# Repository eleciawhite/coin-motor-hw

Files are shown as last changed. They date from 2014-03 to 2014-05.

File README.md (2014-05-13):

coin-motor-hw (Motor Driver Passthrough)
=============
This repository carries the information for fabricating a board that can drive 
a motor with a MOSFET (and pass through other signals)

Some expository and description can be found here: 
http://www.logicalelegance.com/journey/2014/03/releasing-boards/

The original schematic can be found via DigiKey's SchemeIt (which does not 
have layout capabilities at this time):
http://www.digikey.com/schemeit/#fba

The layout was done by Casey Kikendall. (Thank you!)

Pin out:
1 - motor signal
2 - ground
3 - power
4 - passA (I2C SDA)
5 - passB (I2C SCL)

With the N-Channel MOSFET specified in the BOM, a 5V motor can draw a constant 
~270mA (@25C, 210mA @70C). Pulsing the FET or using a higher voltage can lead 
to higher current throughput.

While the MOSFET can pass 60V on the drain side, it turns on at 2V on the 
gate side. (It can go to 20V on the gate side, though I'm driving it with a 
3.3V low current source GPIO.)

This board was designed to work with a 2.7-3.3 V coin-cell style motor (see 
BOM for link to datasheet). This motor has a start up current of 120mA (max) 
and 90mA normal. A more powerful motor could be used with this board.

The pass through signals are (for my project) used for I2C communication to 
a series of accelerometers. However, the are any signals you want to pass 
through.

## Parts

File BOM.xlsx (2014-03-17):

Name | Digikey PN | Quantity | Cost (1) | Link | Note
Motor | 28821-ND | 1 | 3.99 | http://www.digikey.com/product-detail/en/28821/28821-ND/3083191
Schottkey diode | MBRS130LFSCT-ND | 1 | 0.45 | http://www.digikey.com/product-detail/en/MBRS130L/MBRS130LFSCT-ND/3042645
MOSFET | DMN65D8L-7DICT-ND | 1 | 0.17 | http://www.digikey.com/product-detail/en/DMN65D8L-7/DMN65D8L-7DICT-ND/3677916
50kOhm resistor | RMCF1206FT49K9CT-ND | 1 | 0.06 | http://www.digikey.com/scripts/DkSearch/dksus.dll?Detail&itemSeq=146430875&uq=635306656020798143 | Many options, this isn't quite the cheapest
Connectors | 952-2328-ND | 3 | 0.14 | http://www.digikey.com/product-detail/en/M20-9963646/952-2328-ND/3906345 | Many options, this isn't quite the cheapest (also, I went with right angle)
 |  |  | 4.81 | TOTAL (per unit in single quantity)

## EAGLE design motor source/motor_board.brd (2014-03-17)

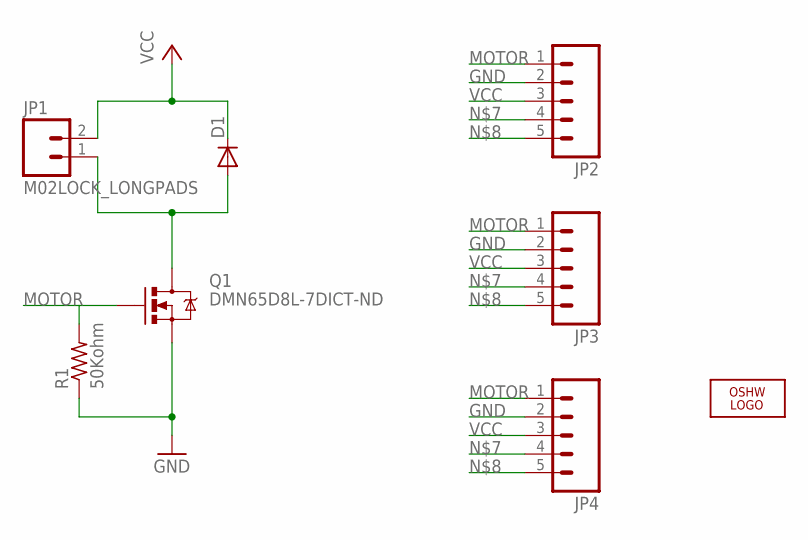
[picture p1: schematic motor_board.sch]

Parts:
D1: DIODE-DO214AA; DO214AA
JP1: M02LOCK_LONGPADS; 1X02_LOCK_LONGPADS
JP2, JP3, JP4: M05PTH; 1X05
LOGO2: OSHW_LOGO_6MILX0100-NT; OSHW_6X100_NOTEXT
Q1: DMN65D8L-7DICT-ND; SOT23
R1: 50Kohm; M1206

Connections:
GND: JP2.2, JP3.2, JP4.2, Q1.2 (S), R1.1
MOTOR: JP2.1, JP3.1, JP4.1, Q1.1 (G), R1.2
unnamed: D1.A, JP1.1, Q1.3 (D)
unnamed: JP2.4, JP3.4, JP4.4
unnamed: JP2.5, JP3.5, JP4.5
VCC: D1.C, JP1.2, JP2.3, JP3.3, JP4.3

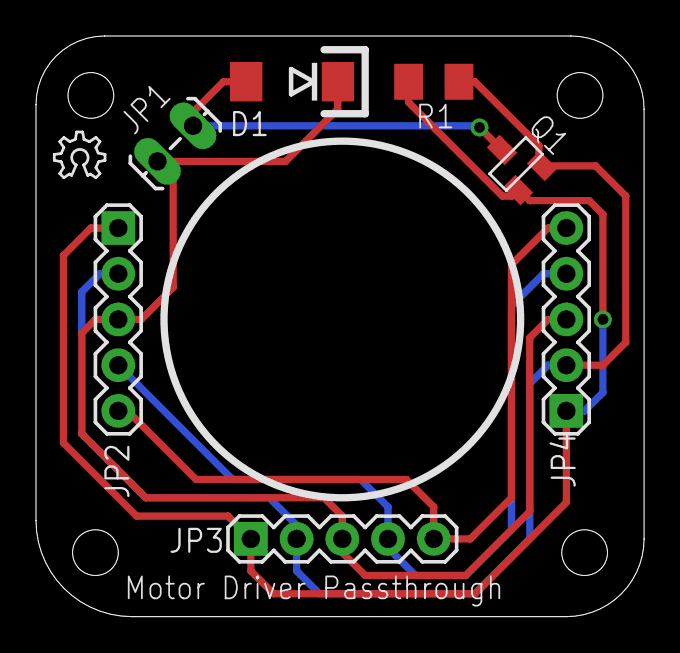
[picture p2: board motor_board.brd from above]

Board: 2 copper layers, 33.8 x 32.3 mm, 8 parts (0 on the bottom side), 6 nets.

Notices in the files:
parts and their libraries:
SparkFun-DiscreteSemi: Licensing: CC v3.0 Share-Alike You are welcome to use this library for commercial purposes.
